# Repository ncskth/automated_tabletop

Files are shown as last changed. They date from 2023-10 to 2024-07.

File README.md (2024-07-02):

### Automated Air Hockey
This repository contains all code and designs required to build and use a remote controlled air hockey table. It has been developed at the NeuroComputing Sciences (NCS) lab at KTH Royal Institute of Technology.

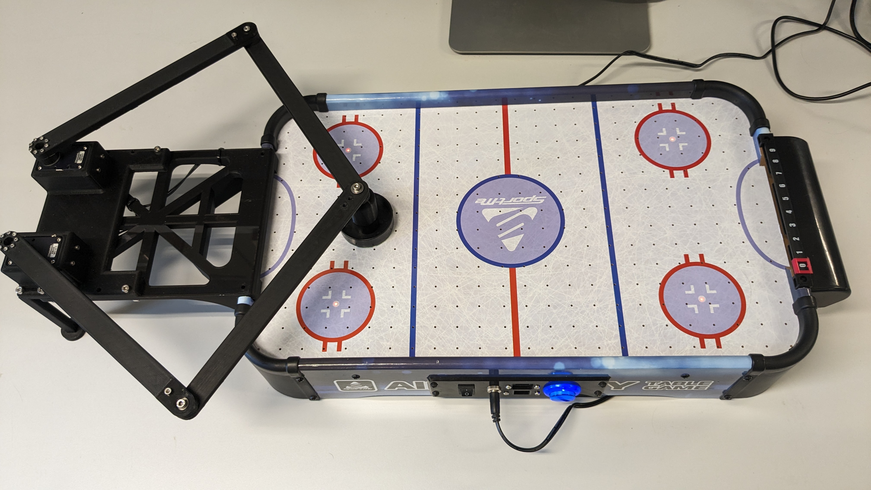
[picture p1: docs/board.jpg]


### Control panel
The whole table is powered with a 12V supply through the 2.1mm barrel jack. For development purposes it is also possible to power the digital control board over USB.

The fan can be toggled on and off with the button.

### Communication
The table can be controlled over both USB and Ethernet.

Attached to the USB-port there is a CH340-chip. Using this on Windows might require installing a driver. The table will show up as a virtual comport and all the settings should match the defaults. The baudrate is 1MBaud.

When ethernet is connected the table hosts a TCP server on port 1337.

Both ethernet and USB use the same communication protocol.

### Protocol
The data protocol follows a simple id-data schema. The ID is a single uint8 and it is immediately followed by N data bytes.

For a reference implementation please see [this script](control_board_fw/test.py)

#### 2 - Handshake
1. ID: 2
1. Length: 0

The control board responds with a 1.

#### 3 - Control
- ID: 3
- Length: 12
- Format
  - [x_pos: float32]
  - [y_pos: float32]
  - [velocity: float32]

Sets the target position and velocity for the handle. The units are in centimeters and centimeters per second. The floats are encoded as standard IEEE.

To run at max velocity, set the velocity to 0.

The control board responds with a 1.

#### 4 - Read position
- ID: 4
- Length: 0

Reads the current handle position. The control boards responds with 2 float32, first the X position and then the Y position for a total of 8 bytes.

#### 5 - Toggle fan
- ID: 5
- Length: 1
- Format
  - [enabled: uint8]

Enables or disables the fan. Any value other than 0 is considered to be true.

The control board responds with a 1.

### Coordinate system
The origin is in between the two servos. The Y-axis follows the board's long side and the X-axis the short side. This means that the handle can be actuated roughly in the rectangle spanned by these points `[(-10, 25), (10, 40)]`

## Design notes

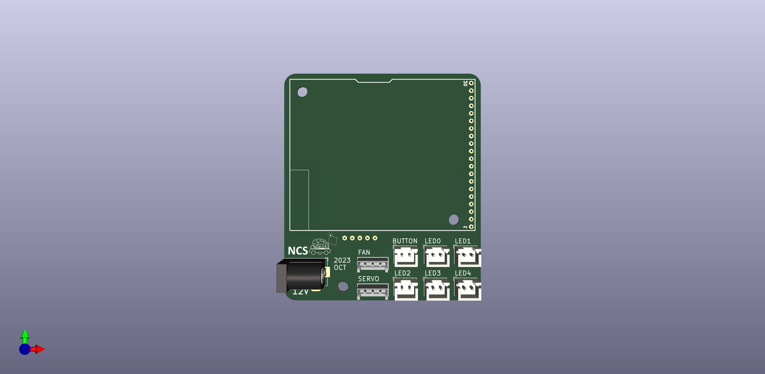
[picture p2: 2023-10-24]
control_board_hw/control_board.png

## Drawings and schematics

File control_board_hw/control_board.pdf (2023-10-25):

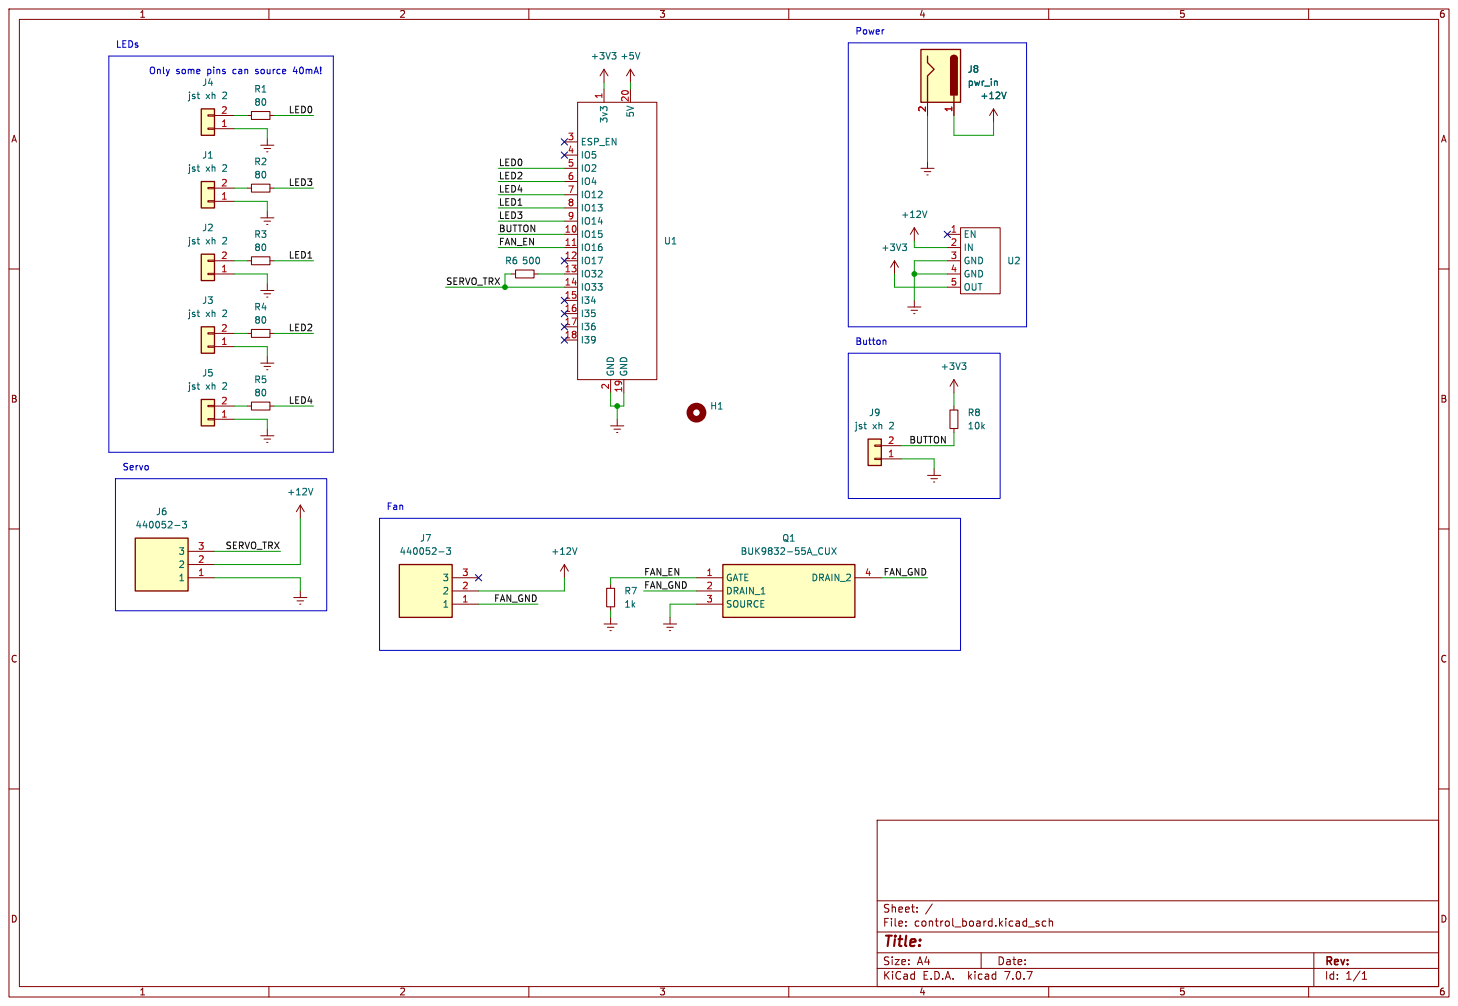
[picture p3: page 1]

2 5V 20 ESP_EN 3
Id: 1/1 Title: File: control_board.kicad_sch Sheet: / 3v3

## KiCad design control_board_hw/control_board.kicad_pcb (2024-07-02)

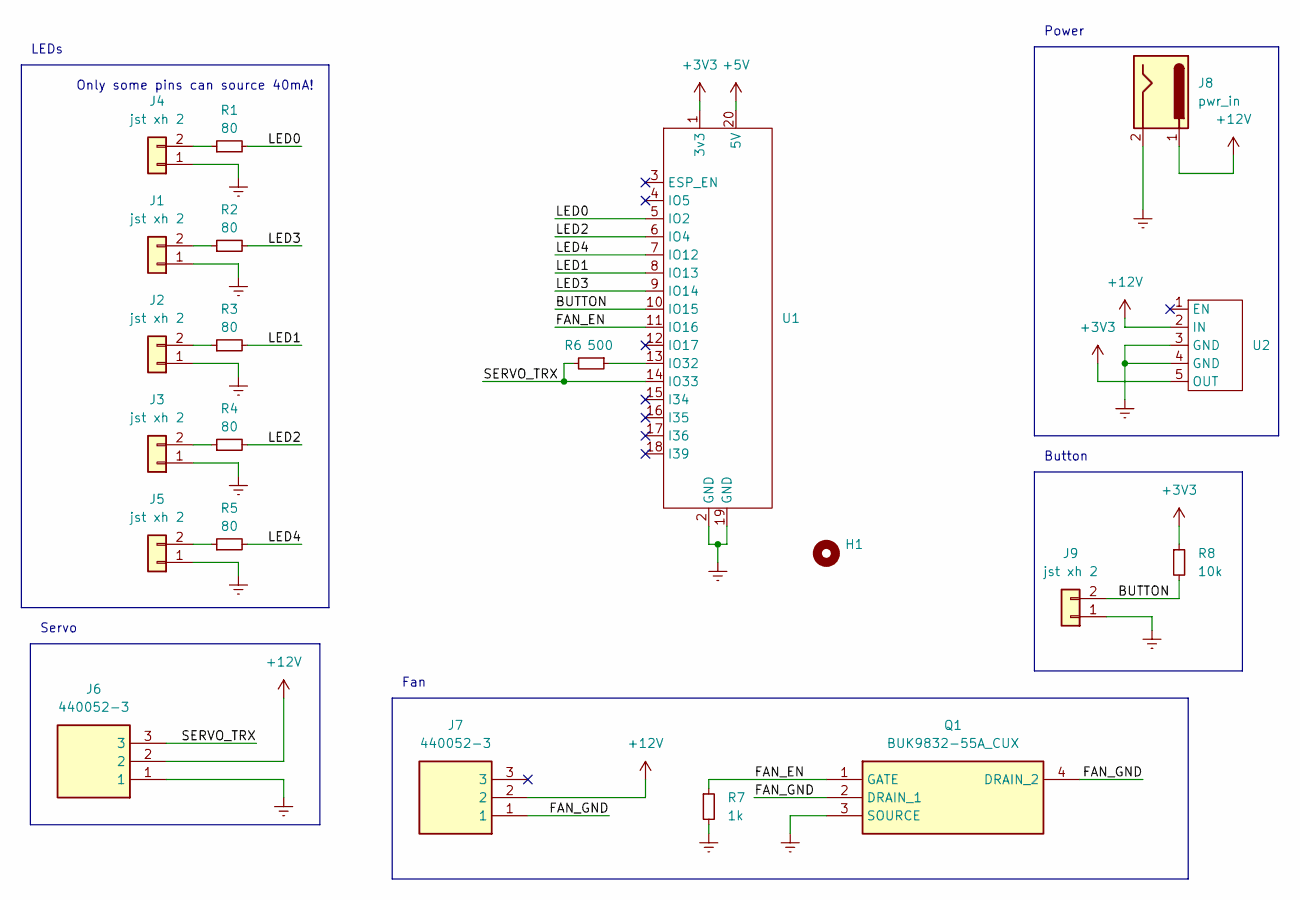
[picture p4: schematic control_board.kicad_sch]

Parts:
H1: MountingHole_Pad; MountingHole_3.5mm
J1, J2, J3, J4, J5, J9: jst xh 2; JST_XH_B2B-XH-A_1x02_P2.50mm_Vertical
J6, J7: 440052-3; SHDR3W64P0X250_1X3_1000X380X630P; Mouser Part Number 571-440052-3
J8: pwr_in; BarrelJack_Horizontal
Q1: BUK9832-55A_CUX; SOT230P700X180-4N; Mouser Part Number 771-BUK9832-55A/CUX
R1, R2, R3, R4, R5: 80; R_0603_1608Metric_Pad0.98x0.95mm_HandSolder
R6: 500; R_0603_1608Metric_Pad0.98x0.95mm_HandSolder
R7: 1k; R_0603_1608Metric_Pad0.98x0.95mm_HandSolder
R8: 10k; R_0603_1608Metric_Pad0.98x0.95mm_HandSolder
U1: esp32-gateway
U2: polulu-durin

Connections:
+3V3: R8.1, U1.1 (3v3), U2.5 (OUT)
+5V: U1.20 (5V)
+12V: J6.2, J7.2, J8.1, U2.2 (IN)
/BUTTON: J9.2, R8.2, U1.10 (IO15)
/FAN_EN: Q1.1 (GATE), R7.1, U1.11 (IO16)
/FAN_GND: J7.1, Q1.2 (DRAIN_1), Q1.4 (DRAIN_2)
/LED0: R1.2, U1.5 (IO2)
/LED1: R3.2, U1.8 (IO13)
/LED2: R4.2, U1.6 (IO4)
/LED3: R2.2, U1.9 (IO14)
/LED4: R5.2, U1.7 (IO12)
/SERVO_TRX: J6.3, R6.2, U1.14 (IO33)
Earth: J1.1, J2.1, J3.1, J4.1, J5.1, J6.1, J8.2, J9.1, Q1.3 (SOURCE), R7.2, U1.2 (GND), U1.19 (GND), U2.3 (GND), U2.4 (GND)
unnamed: J1.2, R2.1
unnamed: J2.2, R3.1
unnamed: J3.2, R4.1
unnamed: J4.2, R1.1
unnamed: J5.2, R5.1
unnamed: R6.1, U1.13 (IO32)

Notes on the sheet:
Only some pins can source 40mA!
Servo
Power
Fan
LEDs
Button

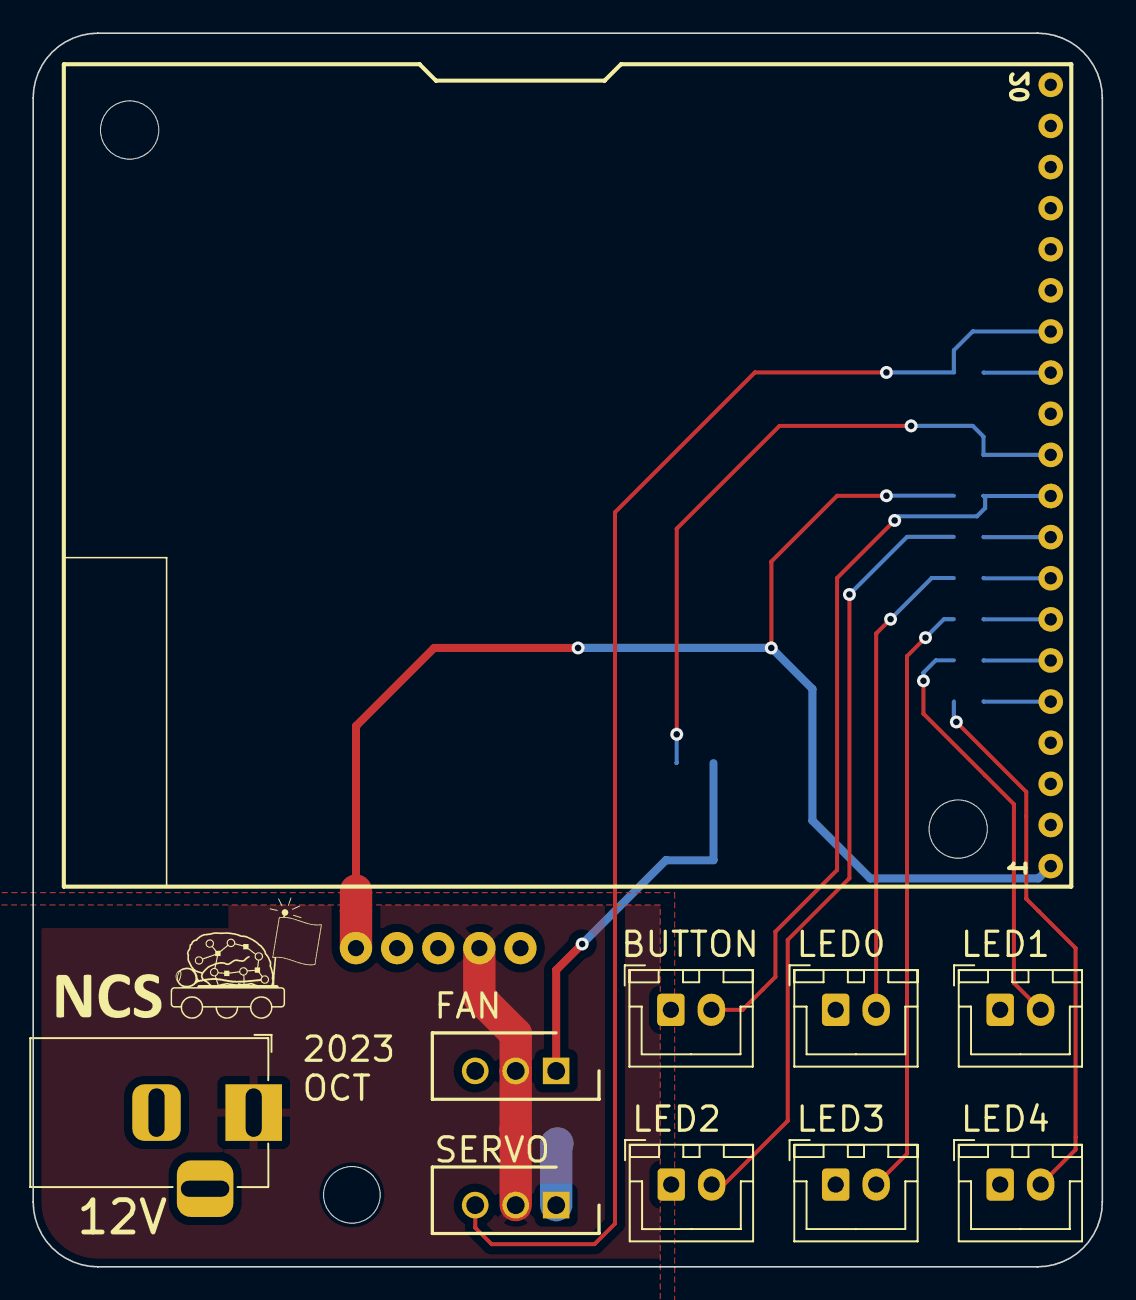
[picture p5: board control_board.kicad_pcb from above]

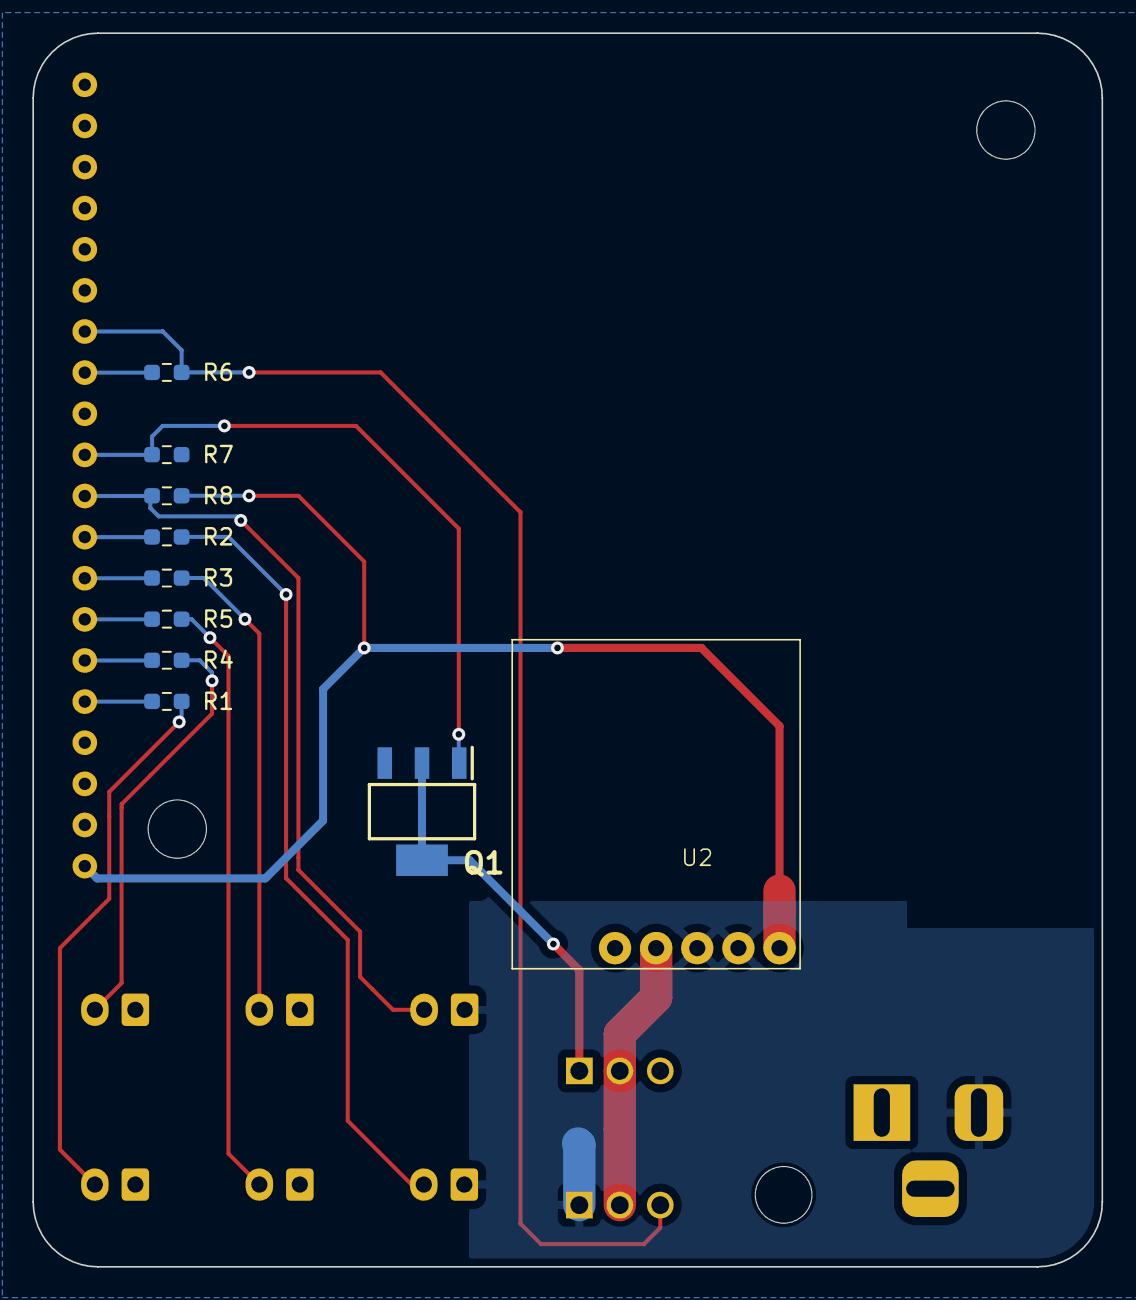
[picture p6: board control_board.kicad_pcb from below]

Board: 2 copper layers, 66.0 x 76.2 mm, 21 parts (10 on the bottom side), 18 nets.

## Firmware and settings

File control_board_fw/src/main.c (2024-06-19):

#include <driver/gpio.h>
#include <driver/ledc.h>
#include <driver/uart.h>
#include <math.h>
#include <stdio.h>
#include <esp_timer.h>
#include <stdbool.h>
#include <esp_log.h>

#include "hardware.h"
#include "dynamixel.h"
#include "networking.h"
#include "five_bar.h"
#include "main.h"
#include "motor.h"
#include "uart.h"

// dynamixel_t dx;

volatile bool fan_enabled;

// int32_t left_trim = 0;
// int32_t right_trim = 0;

void app_main() {
	gpio_reset_pin(GPIO_NUM_2); //default RTS and CTS for uart0
	gpio_reset_pin(GPIO_NUM_4);


    ledc_timer_config_t led_timer_group_conf = {
        .speed_mode = LEDC_LOW_SPEED_MODE,
        .timer_num = LEDC_TIMER_0,
        .duty_resolution = LEDC_TIMER_8_BIT,
        .freq_hz = 5000,
        .clk_cfg = LEDC_APB_CLK};
    ledc_timer_config(&led_timer_group_conf);

    ledc_channel_config_t led_channel_group_conf = {
        .speed_mode = LEDC_LOW_SPEED_MODE,
        .channel = LEDC_CHANNEL_0,
        .timer_sel = 0,
        .intr_type = LEDC_INTR_DISABLE,
        .gpio_num = PIN_LED0,
        .duty = 0,
        .hpoint = 0,
    };

    led_channel_group_conf.gpio_num = PIN_LED0;
    led_channel_group_conf.channel = LEDC_CHANNEL_0;
    ledc_channel_config(&led_channel_group_conf);
    ledc_set_duty(LEDC_LOW_SPEED_MODE, LEDC_CHANNEL_0, 126);
    ledc_update_duty(LEDC_LOW_SPEED_MODE, LEDC_CHANNEL_0);

    led_channel_group_conf.gpio_num = PIN_LED1;
    led_channel_group_conf.channel = LEDC_CHANNEL_1;
    ledc_channel_config(&led_channel_group_conf);
    ledc_set_duty(LEDC_LOW_SPEED_MODE, LEDC_CHANNEL_1, 126);
    ledc_update_duty(LEDC_LOW_SPEED_MODE, LEDC_CHANNEL_1);

    led_channel_group_conf.gpio_num = PIN_LED2;
    led_channel_group_conf.channel = LEDC_CHANNEL_2;
    ledc_channel_config(&led_channel_group_conf);
    ledc_set_duty(LEDC_LOW_SPEED_MODE, LEDC_CHANNEL_2, 126);
    ledc_update_duty(LEDC_LOW_SPEED_MODE, LEDC_CHANNEL_2);


    ledc_timer_config_t led_timer_single_conf = {
        .speed_mode = LEDC_LOW_SPEED_MODE,
        .timer_num = LEDC_TIMER_1,
        .duty_resolution = LEDC_TIMER_8_BIT,
        .freq_hz = 1800,
        .clk_cfg = LEDC_APB_CLK};
    ledc_timer_config(&led_timer_single_conf);

    ledc_channel_config_t led_channel_single_conf = {
        .speed_mode = LEDC_LOW_SPEED_MODE,
        .channel = LEDC_CHANNEL_3,
        .timer_sel = 1,
        .intr_type = LEDC_INTR_DISABLE,
        .gpio_num = PIN_LED3,
        .duty = 0,
        .hpoint = 0,
    };

    ledc_channel_config(&led_channel_single_conf);
    ledc_set_duty(LEDC_LOW_SPEED_MODE, LEDC_CHANNEL_3, 126);
    ledc_update_duty(LEDC_LOW_SPEED_MODE, LEDC_CHANNEL_3);


    ledc_timer_config_t led_timer_button_conf = {
        .speed_mode = LEDC_LOW_SPEED_MODE,
        .timer_num = LEDC_TIMER_2,
        .duty_resolution = LEDC_TIMER_8_BIT,
        .freq_hz = 13000,
        .clk_cfg = LEDC_APB_CLK};
    ledc_timer_config(&led_timer_button_conf);

    ledc_channel_config_t led_channel_button_conf = {
        .speed_mode = LEDC_LOW_SPEED_MODE,
        .channel = LEDC_CHANNEL_4,
        .timer_sel = 2,
        .intr_type = LEDC_INTR_DISABLE,
        .gpio_num = PIN_LED4,
        .duty = 0,
        .hpoint = 0,
    };

    ledc_channel_config(&led_channel_button_conf);
    ledc_set_duty(LEDC_LOW_SPEED_MODE, LEDC_CHANNEL_4, 255);
    ledc_update_duty(LEDC_LOW_SPEED_MODE, LEDC_CHANNEL_4);

    gpio_set_direction(PIN_BUTTON, GPIO_MODE_INPUT);
    gpio_set_direction(PIN_FAN, GPIO_MODE_OUTPUT);
    gpio_set_level(PIN_FAN, 0);

    fan_enabled = false;


    #ifndef LOGGING_ENABLED
    esp_log_level_set("*", ESP_LOG_NONE);		//DISABLE ESP32 LOGGING ON UART0
	gpio_reset_pin(GPIO_NUM_1);
	gpio_reset_pin(GPIO_NUM_3);
    xTaskCreate(uart_thread, "uart_thread", 4086, NULL, 5, NULL);
    #endif
    xTaskCreate(motor_thread, "motor_thread", 4086, NULL, 5, NULL);
    xTaskCreate(tcp_server_thread, "tcp_server_thread", 4086, NULL, 5, NULL);

    printf("Initialised\n");

    while (true) {
        bool level = gpio_get_level(PIN_BUTTON);
        static int64_t last_toggled = 0;
        if (level == 0 && esp_timer_get_time() - last_toggled > 1e6) {
            fan_enabled = !fan_enabled;
            last_toggled = esp_timer_get_time();
            gpio_set_level(PIN_FAN, fan_enabled);
        }
        vTaskDelay(10);
    }
}

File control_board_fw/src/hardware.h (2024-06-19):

#define PIN_LED0 13
#define PIN_LED1 4
#define PIN_LED2 14
#define PIN_LED3 12
#define PIN_LED4 2

#define PIN_BUTTON 15
#define PIN_FAN 16
#define PIN_SERVO_RX 33
#define PIN_SERVO_TX 32
#define NUM_UART_SERVO UART_NUM_1
#define BAUD_UARD_SERVO 1000000

#define NUM_UART_CONSOLE UART_NUM_0
#define BAUD_UARD_CONSOLE 1000000

#define PI 3.1415

#define R1 23
#define R2 23
#define R3 23
#define R4 23
#define R5 10

#define LEFT_ID 1
#define RIGHT_ID 2

#define BOARD_LEFT_LIM -11
#define BOARD_RIGHT_LIM 11
#define BOARD_BOT_LIM 23
#define BOARD_TOP_LIM 44

// #define LOGGING_ENABLED

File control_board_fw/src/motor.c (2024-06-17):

#include <driver/uart.h>
#include <math.h>
#include <stdio.h>
#include <esp_timer.h>
#include <stdbool.h>

#include "motor.h"
#include "dynamixel.h"
#include "hardware.h"
#include "five_bar.h"

dynamixel_t dx;

volatile float wanted_pos_x = 0;
volatile float wanted_pos_y = 30;
volatile float wanted_velocity = 50;
volatile float current_pos_x = 0;
volatile float current_pos_y = 0;
const float time_step = 0.001;
const float overshoot = time_step * 3;

volatile int32_t left_trim = 0;
volatile int32_t right_trim = 0;

void motor_thread() {
    uart_config_t uart_servo = {
        .baud_rate = BAUD_UARD_SERVO,
        .data_bits = UART_DATA_8_BITS,
        .parity = UART_PARITY_DISABLE,
        .stop_bits = UART_STOP_BITS_1,
        .flow_ctrl = UART_HW_FLOWCTRL_DISABLE,
    };

    uart_param_config(1, &uart_servo);
    uart_set_pin(NUM_UART_SERVO, PIN_SERVO_TX, PIN_SERVO_RX, -1, -1);
    uart_driver_install(NUM_UART_SERVO, 512, 512, 20, NULL, 0);
    vTaskDelay(200);

    float virtual_current_pos_x = wanted_pos_x;
    float virtual_current_pos_y = wanted_pos_y;
    float real_current_pos_x = 0;
    float real_current_pos_y = 0;
    static const int32_t center = 4095 / 2;
    int32_t real_current_discrete_left = 0;
    int32_t real_current_discrete_right = 0;
    int32_t virtual_current_discrete_left = 0;
    int32_t virtual_current_discrete_right = 0;
    int32_t last_update = esp_timer_get_time();
    dx_init(&dx, NUM_UART_SERVO);

    dx_restart(&dx, LEFT_ID);
    dx_restart(&dx, RIGHT_ID);
    vTaskDelay(1000);

    dx_set_status_return_level(&dx, DX_ID_BROADCAST, DX_PING_READ);
    dx_set_operating_mode(&dx, LEFT_ID, DX_POSITION_CONTROL);
    dx_set_operating_mode(&dx, RIGHT_ID, DX_POSITION_CONTROL);
    dx_enable_torque(&dx, LEFT_ID, true);
    dx_enable_torque(&dx, RIGHT_ID, true);

    dx_set_profile_velocity_raw(&dx, LEFT_ID, 100);
    dx_set_profile_velocity_raw(&dx, RIGHT_ID, 100);
    vTaskDelay(500);

    float l,r;

    five_bar_pos_to_angle(R1, R2, R3, R4, R5, virtual_current_pos_x, virtual_current_pos_y, &l, &r);

    float this_step_left_adjusted = -(PI / 2 - l);
    float this_step_right_adjusted = -(PI / 2 - r);

    int32_t left_discrete = center + this_step_left_adjusted / (2 * PI) * 4095 + left_trim;
    int32_t right_discrete = center + this_step_right_adjusted / (2 * PI) * 4095 + right_trim;

    dx_set_goal_position(&dx, LEFT_ID, left_discrete, false);
    dx_set_goal_position(&dx, RIGHT_ID, right_discrete, false);
    vTaskDelay(1000);
    virtual_current_discrete_left = left_discrete;
    virtual_current_discrete_right = right_discrete;
    dx_set_profile_velocity_raw(&dx, LEFT_ID, 0);
    dx_set_profile_velocity_raw(&dx, RIGHT_ID, 0);
    vTaskDelay(100);
    last_update = esp_timer_get_time();
    while (true) {
        float scale = 1;
        if (wanted_pos_x < BOARD_LEFT_LIM) {
            wanted_pos_x = BOARD_LEFT_LIM;
        }
        if (wanted_pos_x > BOARD_RIGHT_LIM) {
            wanted_pos_x = BOARD_RIGHT_LIM;
        }
        if (wanted_pos_y < BOARD_BOT_LIM) {
            wanted_pos_y = BOARD_BOT_LIM;
        }
        if (wanted_pos_y > BOARD_TOP_LIM) {
            wanted_pos_y = BOARD_TOP_LIM;
        }


        float wanted_delta_x = wanted_pos_x - virtual_current_pos_x;
        float wanted_delta_y = wanted_pos_y - virtual_current_pos_y;

        float wanted_delta_abs = sqrtf(wanted_delta_x * wanted_delta_x + wanted_delta_y * wanted_delta_y);

        float total_move_time = wanted_delta_abs / wanted_velocity;

        float step_move_time = total_move_time > time_step + overshoot ? time_step + overshoot : total_move_time;

        float this_step_delta_x = wanted_delta_x * step_move_time / total_move_time;
        float this_step_delta_y = wanted_delta_y * step_move_time / total_move_time;

        if (total_move_time == 0) {
            this_step_delta_x = 0;
            this_step_delta_y = 0;
            goto readback;
        }

        float this_step_pos_x = virtual_current_pos_x + this_step_delta_x;
        float this_step_pos_y = virtual_current_pos_y + this_step_delta_y;

        float this_step_left_angle;
        float this_step_right_angle;
        five_bar_pos_to_angle(R1, R2, R3, R4, R5, this_step_pos_x, this_step_pos_y, &this_step_left_angle, &this_step_right_angle);

        float this_step_left_adjusted = -(PI / 2 - this_step_left_angle);
        float this_step_right_adjusted = -(PI / 2 - this_step_right_angle);

        int32_t this_step_left_discrete = center + this_step_left_adjusted / (2 * PI) * 4095 + left_trim;
        int32_t this_step_right_discrete = center + this_step_right_adjusted / (2 * PI) * 4095 + right_trim;

        // speed calculations seem to be unnecessary :/

        // int32_t this_step_discrete_delta_left = this_step_left_discrete - virtual_current_discrete_left;
        // int32_t this_step_discrete_delta_right = this_step_right_discrete - virtual_current_discrete_right;
        // virtual_current_discrete_left = this_step_left_discrete;
        // virtual_current_discrete_right = this_step_right_discrete;

        // float steps_per_second_left = this_step_discrete_delta_left / step_move_time;
        // float steps_per_second_right = this_step_discrete_delta_right / step_move_time;

        // static const float steps_per_second_to_rpm = 360 * 60.0 / 4095.0;

        // int32_t left_speed_discrete = steps_per_second_left * steps_per_second_to_rpm * 0.02; // magic constant from dynamixel docs
        // int32_t right_speed_discrete = steps_per_second_right * steps_per_second_to_rpm * 0.02;
        // printf("bajs %d\n", left_speed_discrete);
        // left_speed_discrete = abs(left_speed_discrete) < 1 ? 1 : abs(left_speed_discrete);
        // right_speed_discrete = abs(right_speed_discrete) < 1 ? 1 : abs(right_speed_discrete);

        // left_speed_discrete = abs(left_speed_discrete) > 32767 ? 32767 : abs(left_speed_discrete);
        // right_speed_discrete = abs(right_speed_discrete) > 32767 ? 32767 : abs(right_speed_discrete);


        // left_speed_discrete = 0;
        // right_speed_discrete = 0;

        // dx_set_profile_velocity_raw(&dx, LEFT_ID, left_speed_discrete);
        // dx_set_profile_velocity_raw(&dx, RIGHT_ID, right_speed_discrete);

        // printf("wanted speed %ld %ld\n", left_speed_discrete, right_speed_discrete);
        // printf("wanted angul %f %f\n", this_step_left_angle, this_step_right_angle);
        // printf("wanted disco %ld %ld\n", this_step_left_discrete, this_step_right_discrete);
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

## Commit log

2023-09-13 fix default motor
2023-10-24 control board v1
    [control_board.kicad_pcb, control_board.kicad_sch]
2023-10-25 finish control board
    [control_board.kicad_pcb, control_board.kicad_sch]
2024-03-05 fix velocity and position read back
    [dynamixel.c, dynamixel.h, main.c]
2024-06-19 fix LED
2024-07-02 better README
    [control_board.kicad_pcb, control_board.kicad_sch]
